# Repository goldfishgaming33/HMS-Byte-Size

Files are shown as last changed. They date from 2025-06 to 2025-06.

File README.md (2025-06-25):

# ABOUT

- I decided to take on this project when I realised I had nothing better to do over the summer
- I wanted to make use of skills I learnt while building a different device for a school competition which was a satellite in the size of a can
- I learnt to solder better, code better on the Raspberry Pi platform and design a PCB
- RC models and boats have always interested me, so I decided to combine the two to create HMS Byte Size
- The system will operate on the Raspberry Pi Zero 2W, communicating over 2.4GHz RF with a secondary Pi which will control the boat remotely
- I wasn't too confident with SMD and lacking a hot plate or any SMD capability, I decided to go with all through hole components

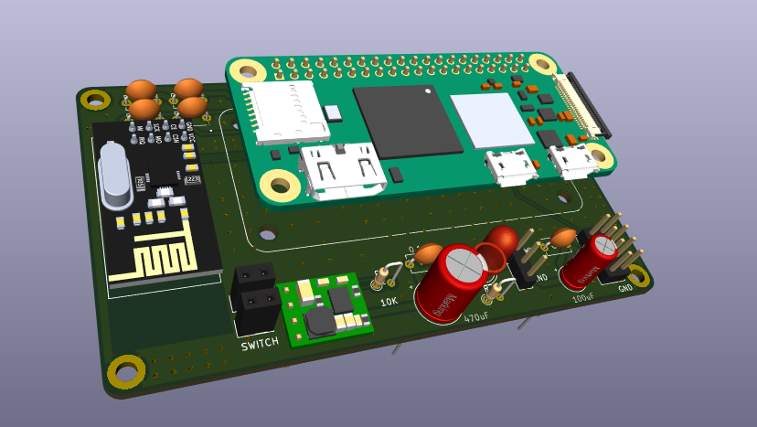
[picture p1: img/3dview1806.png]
3Dview

_LED will power to confirm the board is running_

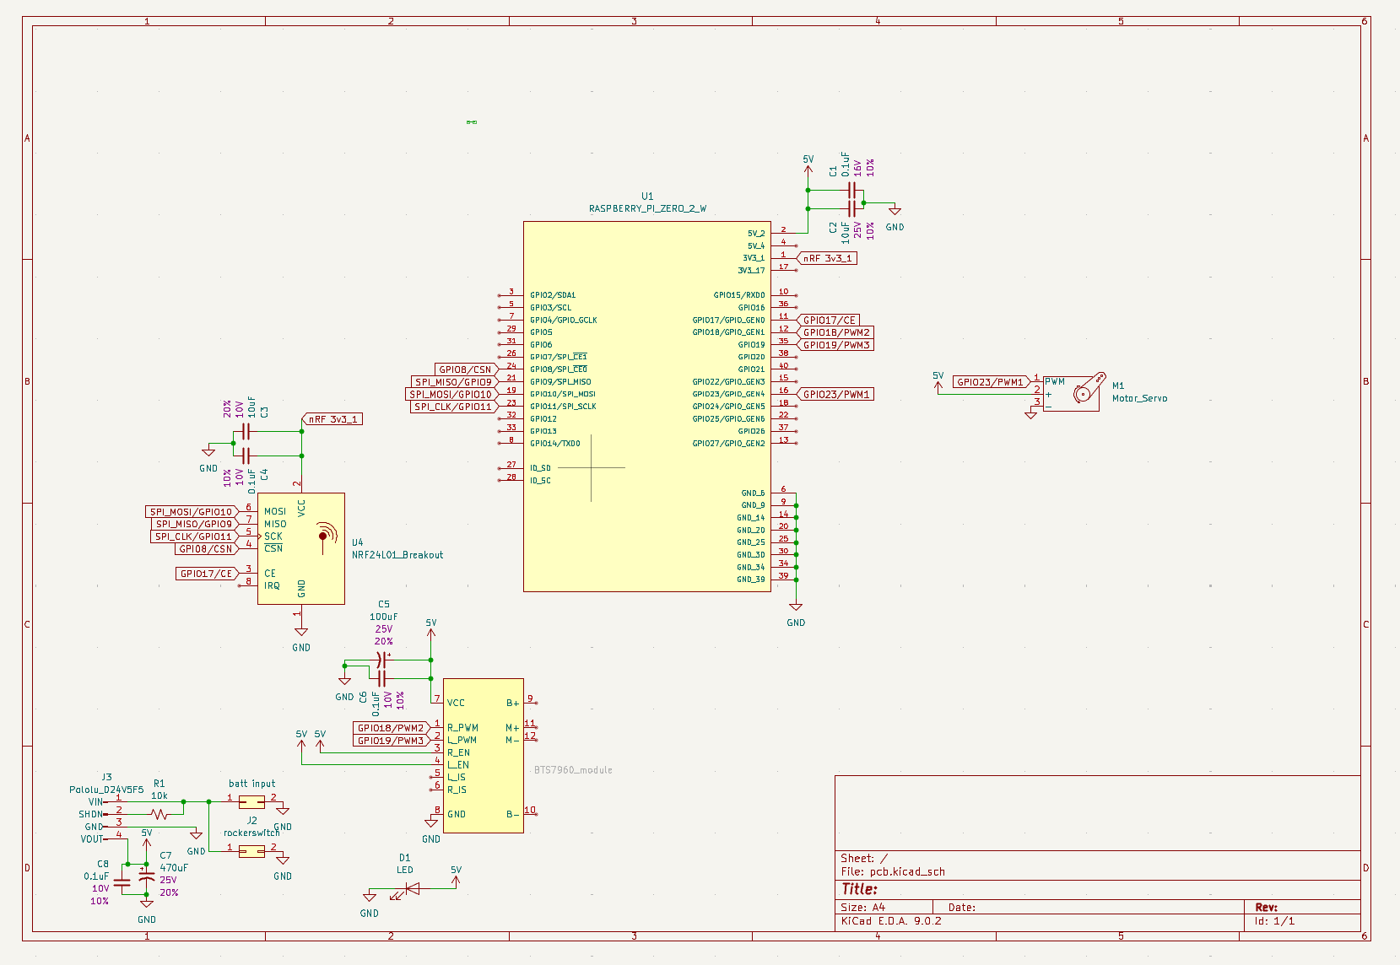
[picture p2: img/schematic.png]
schem

_Careful planning of how to power such project took place and resulted in numerous de-coupling capacitors, and others to manage current spikes and back-EMI_

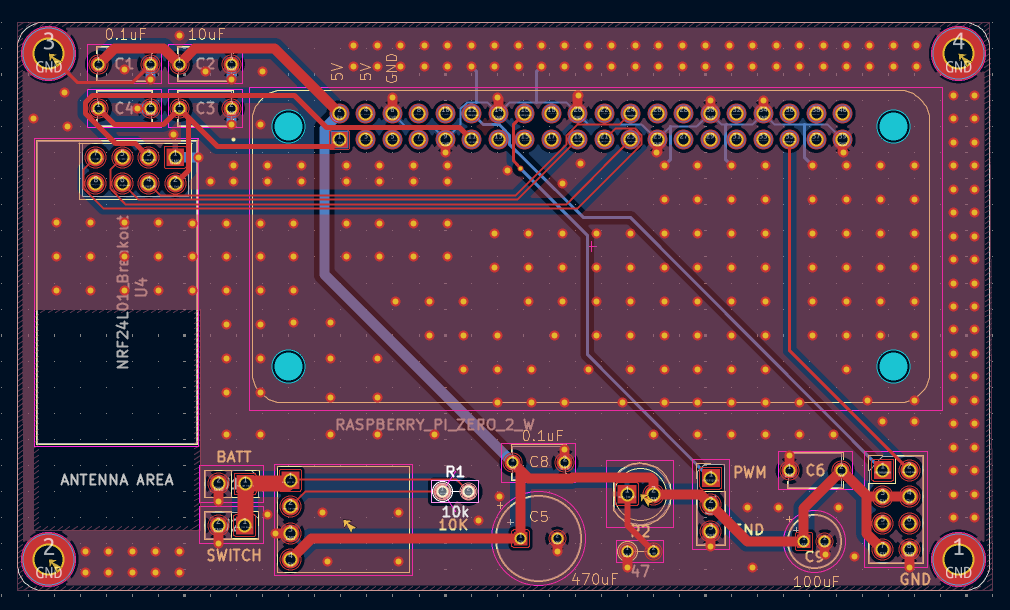
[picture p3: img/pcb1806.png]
pcb

_2-layer PCB composed of all through hole components, will full layer ground pours, and via stitching_

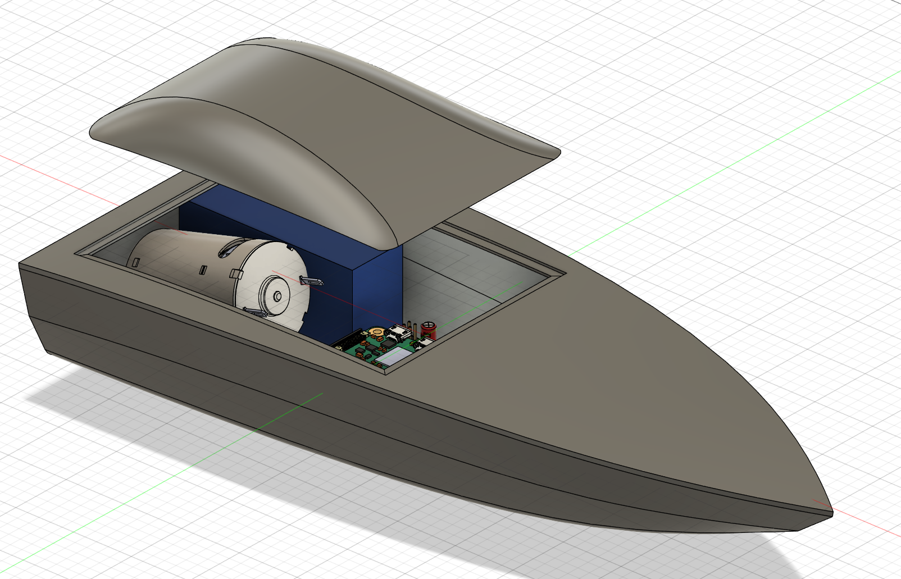
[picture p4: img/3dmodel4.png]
3dmodel

_Compact 3D printed design for easy assembly_

## Costs
It's looking rather costly

I've tried to stick to amazon and ali express for cheap components, but obviously I have doubts about reliability and whatnot.

Things like resistors and capacitors through MouserUK and RapidElectronics

## BOM

It's a bit messy, I just add as I go. All accurate though

https://1drv.ms/x/c/58d29176c16c150d/ESuSnoqv2EdMtOshy8H60zMBzeC2gvnFj-rfRvqEexovow?e=tm9gPX

Screenshot
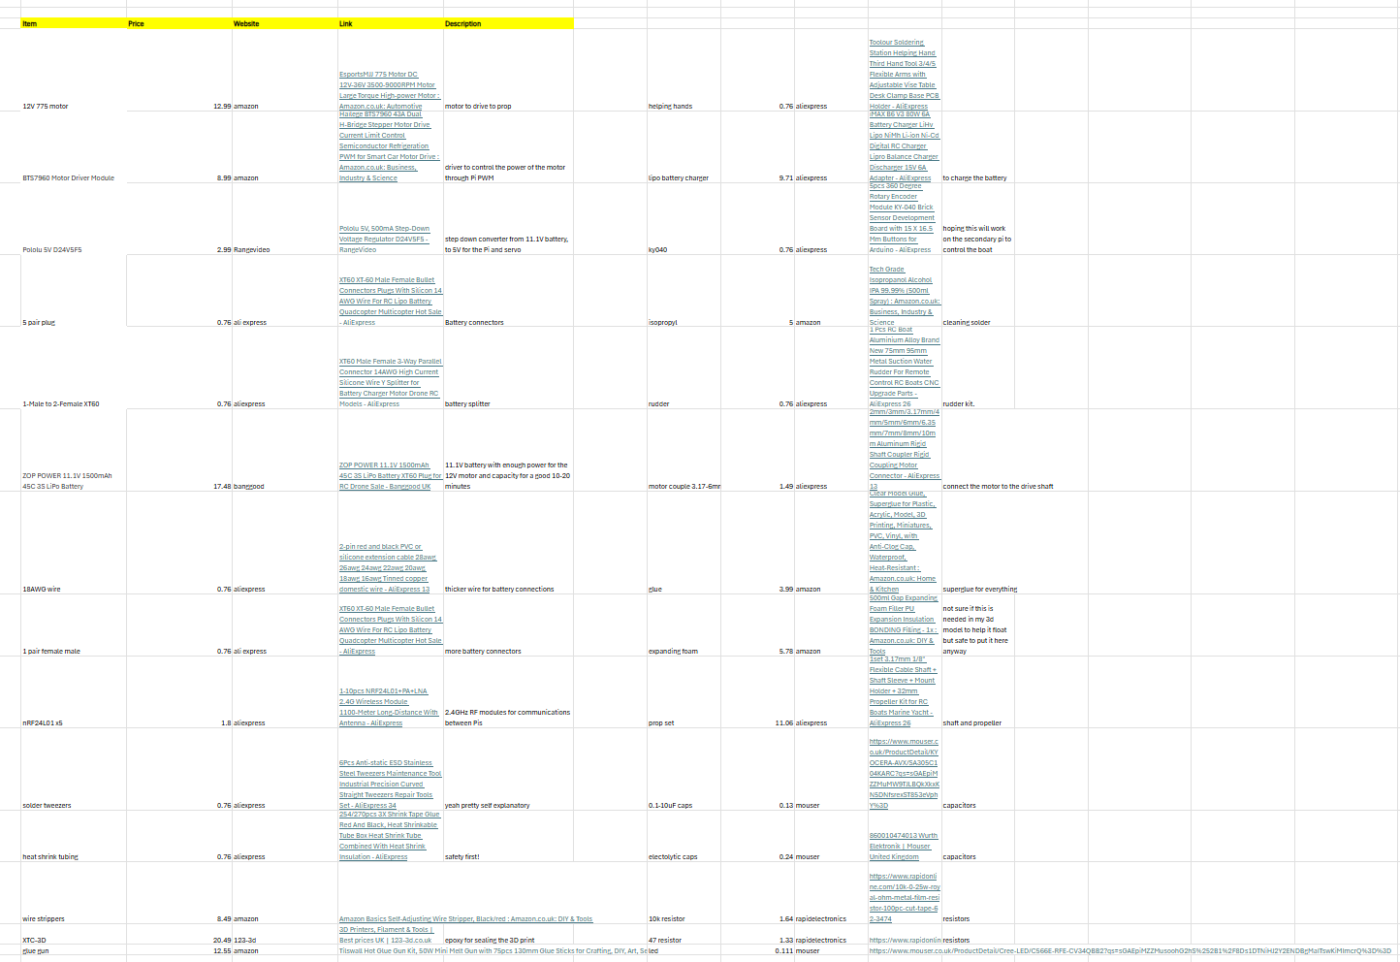
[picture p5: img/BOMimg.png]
BOM


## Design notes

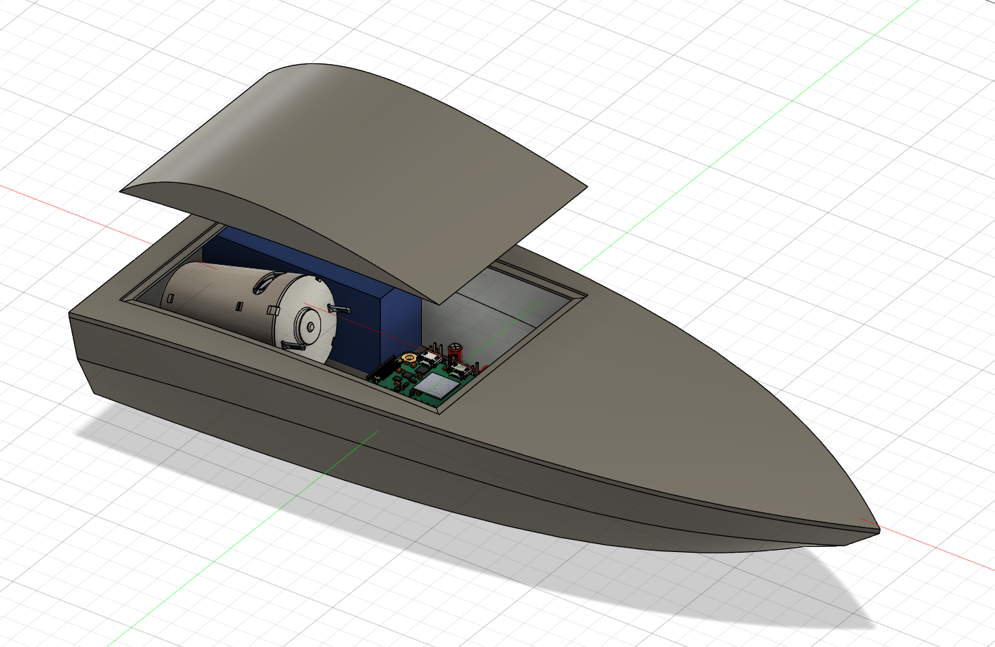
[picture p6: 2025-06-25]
img/3dmodel3.png

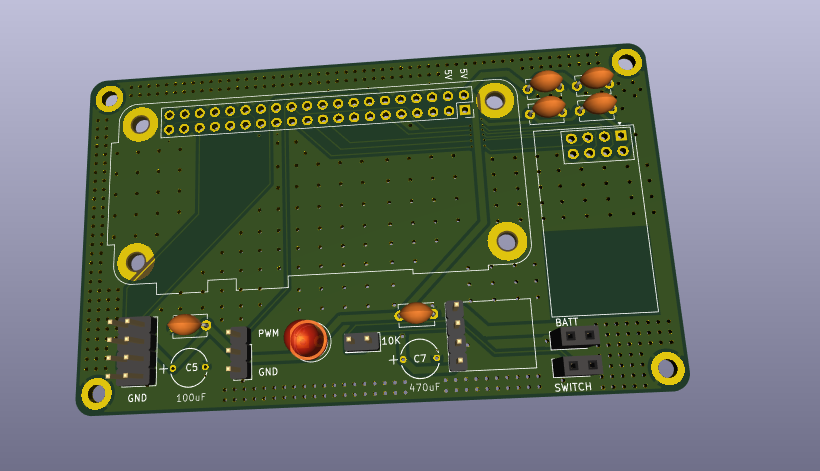
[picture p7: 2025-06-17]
img/3Dview.png

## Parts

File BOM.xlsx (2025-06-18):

Item | Price | Website | Link | Description
12V 775 motor | 12.99 | amazon | EsportsMJJ 775 Motor DC 12V-36V 3500-9000RPM Motor Large Torque High-power Motor : Amazon.co.uk: Automotive (https://www.amazon.co.uk/EsportsMJJ-12V-36V-3500-9000RPM-Torque-High-power/dp/B075D85KVV) | motor to drive to prop |  | helping hands | 0.76 | aliexpress | Toolour Soldering Station Helping Hand Third Hand Tool 3/4/5 Flexible Arms with Adjustable Vise Table Desk Clamp Base PCB Holder - AliExpress (https://www.aliexpress.com/item/1005007513733434.html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)
BTS7960 Motor Driver Module | 8.99 | amazon | Hailege BTS7960 43A Dual H-Bridge Stepper Motor Drive Current Limit Control Semiconductor Refrigeration PWM for Smart Car Motor Drive : Amazon.co.uk: Business, Industry & Science (https://www.amazon.co.uk/BTS7960-H-Bridge-Stepper-Semiconductor-Refrigeration/dp/B07Y4TTK3Z) | driver to control the power of the motor through Pi PWM |  | lipo battery charger | 9.71 | aliexpress | iMAX B6 V3 80W 6A Battery Charger LiHv Lipo NiMh Li-ion Ni-Cd Digital RC Charger Lipro Balance Charger Discharger 15V 6A Adapter - AliExpress (https://www.aliexpress.com/item/1005005231331856.html?businessType=ProductDetail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) | to charge the battery
Pololu 5V D24V5F5 | 2.99 | Rangevideo | Pololu 5V, 500mA Step-Down Voltage Regulator D24V5F5 - RangeVideo (https://www.rangevideo.com/products/pololu-5v-500ma-step-down-voltage-regulator-d24v5f5) | step down converter from 11.1V battery, to 5V for the Pi and servo |  | ky040 | 0.76 | aliexpress | 5pcs 360 Degree Rotary Encoder Module KY-040 Brick Sensor Development Board with 15 X 16.5 Mm Buttons for Arduino - AliExpress (https://www.aliexpress.com/item/1005005559054521.html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) | hoping this will work on the secondary pi to control the boat
5 pair plug | 0.76 | ali express | XT60 XT-60 Male Female Bullet Connectors Plugs With Silicon 14 AWG Wire For RC Lipo Battery Quadcopter Multicopter Hot Sale - AliExpress (https://www.aliexpress.com/item/1005003658392996.html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) | Battery connectors |  | isopropyl | 5 | amazon | Tech Grade Isopropanol Alcohol IPA 99.99% (500ml Spray) : Amazon.co.uk: Business, Industry & Science (https://www.amazon.co.uk/Grade-Isopropanol-Alcohol-99-99-500ml/dp/B08PD9P1VX) | cleaning solder
1-Male to 2-Female XT60 | 0.76 | aliexpress | XT60 Male Female 3-Way Parallel Connector 14AWG High Current Silicone Wire Y Splitter for Battery Charger Motor Drone RC Models - AliExpress (https://www.aliexpress.com/item/1005005725141150.html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) | battery splitter |  | rudder | 0.76 | aliexpress | 1 Pcs RC Boat Aluminium Alloy Brand New 75mm 95mm Metal Suction Water Rudder For Remote Control RC Boats CNC Upgrade Parts - AliExpress 26 (https://www.aliexpress.com/item/1005005873906106.html?businessType=ProductDetail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) | rudder kit.
ZOP POWER 11.1V 1500mAh 45C 3S LiPo Battery | 17.48 | banggood | ZOP POWER 11.1V 1500mAh 45C 3S LiPo Battery XT60 Plug for RC Drone Sale - Banggood UK (https://uk.banggood.com/ZOP-POWER-11_1V-1500mAh-45C-3S-LiPo-Battery-XT60-Plug-for-RC-Drone-p-1979030.html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) | 11.1V battery with enough power for the 12V motor and capacity for a good 10-20 minutes |  | motor couple 3.17-6mm | 1.49 | aliexpress | 2mm/3mm/3.17mm/4mm/5mm/6mm/6.35mm/7mm/8mm/10mm Aluminum Rigid Shaft Coupler Rigid Coupling Motor Connector - AliExpress 13 (https://www.aliexpress.com/item/4000196552485.html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) | connect the motor to the drive shaft
18AWG wire | 0.76 | aliexpress | 2-pin red and black PVC or silicone extension cable 28awg 26awg 24awg 22awg 20awg 18awg 16awg Tinned copper domestic wire - AliExpress 13 (https://www.aliexpress.com/item/1005007251965003.html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) | thicker wire for battery connections |  | glue | 3.99 | amazon | Plastic Glue 30 g, Clear Model Glue, Superglue for Plastic, Acrylic, Model, 3D Printing, Miniatures, PVC, Vinyl, with Anti-Clog Cap, Waterproof, Heat-Resistant : Amazon.co.uk: Home & Kitchen (https://www.amazon.co.uk/Superglue-Miniatures-Anti-Clog-Waterproof-Heat-Resistant/dp/B0DRJNFVZ9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) | superglue for everything
1 pair female male | 0.76 | ali express | XT60 XT-60 Male Female Bullet Connectors Plugs With Silicon 14 AWG Wire For RC Lipo Battery Quadcopter Multicopter Hot Sale - AliExpress (https://www.aliexpress.com/item/1005003658392996.html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) | more battery connectors |  | expanding foam | 5.78 | amazon | 500ml Gap Expanding Foam Filler PU Expansion Insulation BONDING Filling - 1x : Amazon.co.uk: DIY & Tools (https://www.amazon.co.uk/Expanding-Expansion-Insulation-BONDING-Filling/dp/B093DZT8TZ) | not sure if this is needed in my 3d model to help it float but safe to put it here anyway
nRF24L01 x5 | 1.8 | aliexpress | 1-10pcs NRF24L01+PA+LNA 2.4G Wireless Module 1100-Meter Long-Distance With Antenna - AliExpress (https://www.aliexpress.com/item/1005007796985331.html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) | 2.4GHz RF modules for communications between Pis |  | prop set | 11.06 | aliexpress | 1set 3.17mm 1/8" Flexible Cable Shaft + Shaft Sleeve + Mount Holder + 32mm Propeller Kit for RC Boats Marine Yacht - AliExpress 26 (https://www.aliexpress.com/item/1005001349058436.html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) | shaft and propeller
solder tweezers | 0.76 | aliexpress | 6Pcs Anti-static ESD Stainless Steel Tweezers Maintenance Tool Industrial Precision Curved Straight Tweezers Repair Tools Set - AliExpress 34 (https://www.aliexpress.com/item/1005007425589207.html?mp=1) | yeah pretty self explanatory |  | 0.1-10uF caps | 0.13 | mouser | https://www.mouser.co.uk/ProductDetail/KYOCERA-AVX/SA305C104KARC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 | capacitors
heat shrink tubing | 0.76 | aliexpress | 254/270pcs 3X Shrink Tape Glue Red And Black, Heat Shrinkable Tube Box Heat Shrink Tube Combined With Heat Shrink Insulation - AliExpress (https://www.aliexpress.com/item/1005006511088545.html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) | safety first! |  | electolytic caps | 0.24 | mouser | 860010474013 Wurth Elektronik | Mouser United Kingdom (https://www.mouser.co.uk/ProductDetail/Wurth-Elektronik/860010474013?qs=0KOYDY2FL2%2Ftqmj8vEDl2w%3D%3D) | capacitors
wire strippers | 8.49 | amazon | Amazon Basics Self-Adjusting Wire Stripper, Black/red : Amazon.co.uk: DIY & Tools (https://www.amazon.co.uk/AmazonBasics-DS-SWP-Self-Adjusting-Wire-Stripper/dp/B07TS6KCXD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) |  |  | 10k resistor | 1.64 | rapidelectronics | https://www.rapidonline.com/10k-0-25w-royal-ohm-metal-film-resistor-100pc-cut-tape-62-3474 | resistors
XTC-3D | 20.49 | 123-3d | 3D Printers, Filament & Tools | Best prices UK | 123-3d.co.uk (https://www.123-3d.co.uk/SmoothOn-Smooth-On-XTC-3D-coating-181-gr-A-B-i8654.html) | epoxy for sealing the 3D print |  | 47 resistor | 1.33 | rapidelectronics | https://www.rapidonline.com/47r-0-25w-royal-ohm-metal-film-resistor-100pc-cut-tape-62-3418 | resistors
glue gun | 12.55 | amazon | Tilswall Hot Glue Gun Kit, 50W Mini Melt Gun with 75pcs 130mm Glue Sticks for Crafting, DIY, Art, Sealing, Home Repairs, Cards, and Glass : Amazon.co.uk: DIY & Tools (https://www.amazon.co.uk/Tilswall-Quickly-Patents-Sealing-Repairs/dp/B07TD35L5R?sp_csd=d2lkZ2V0TmFtZT1zcF9hdGY) |  |  | led | 0.111 | mouser | https://www.mouser.co.uk/ProductDetail/Cree-LED/C566E-RFE-CV34QBB2
 |  |  |  |  | Mfr Part Number | Manufacturer Part Number | Mouser Part Number | Manufacturer Name | Description | Quantity 1 | Unit Price 1

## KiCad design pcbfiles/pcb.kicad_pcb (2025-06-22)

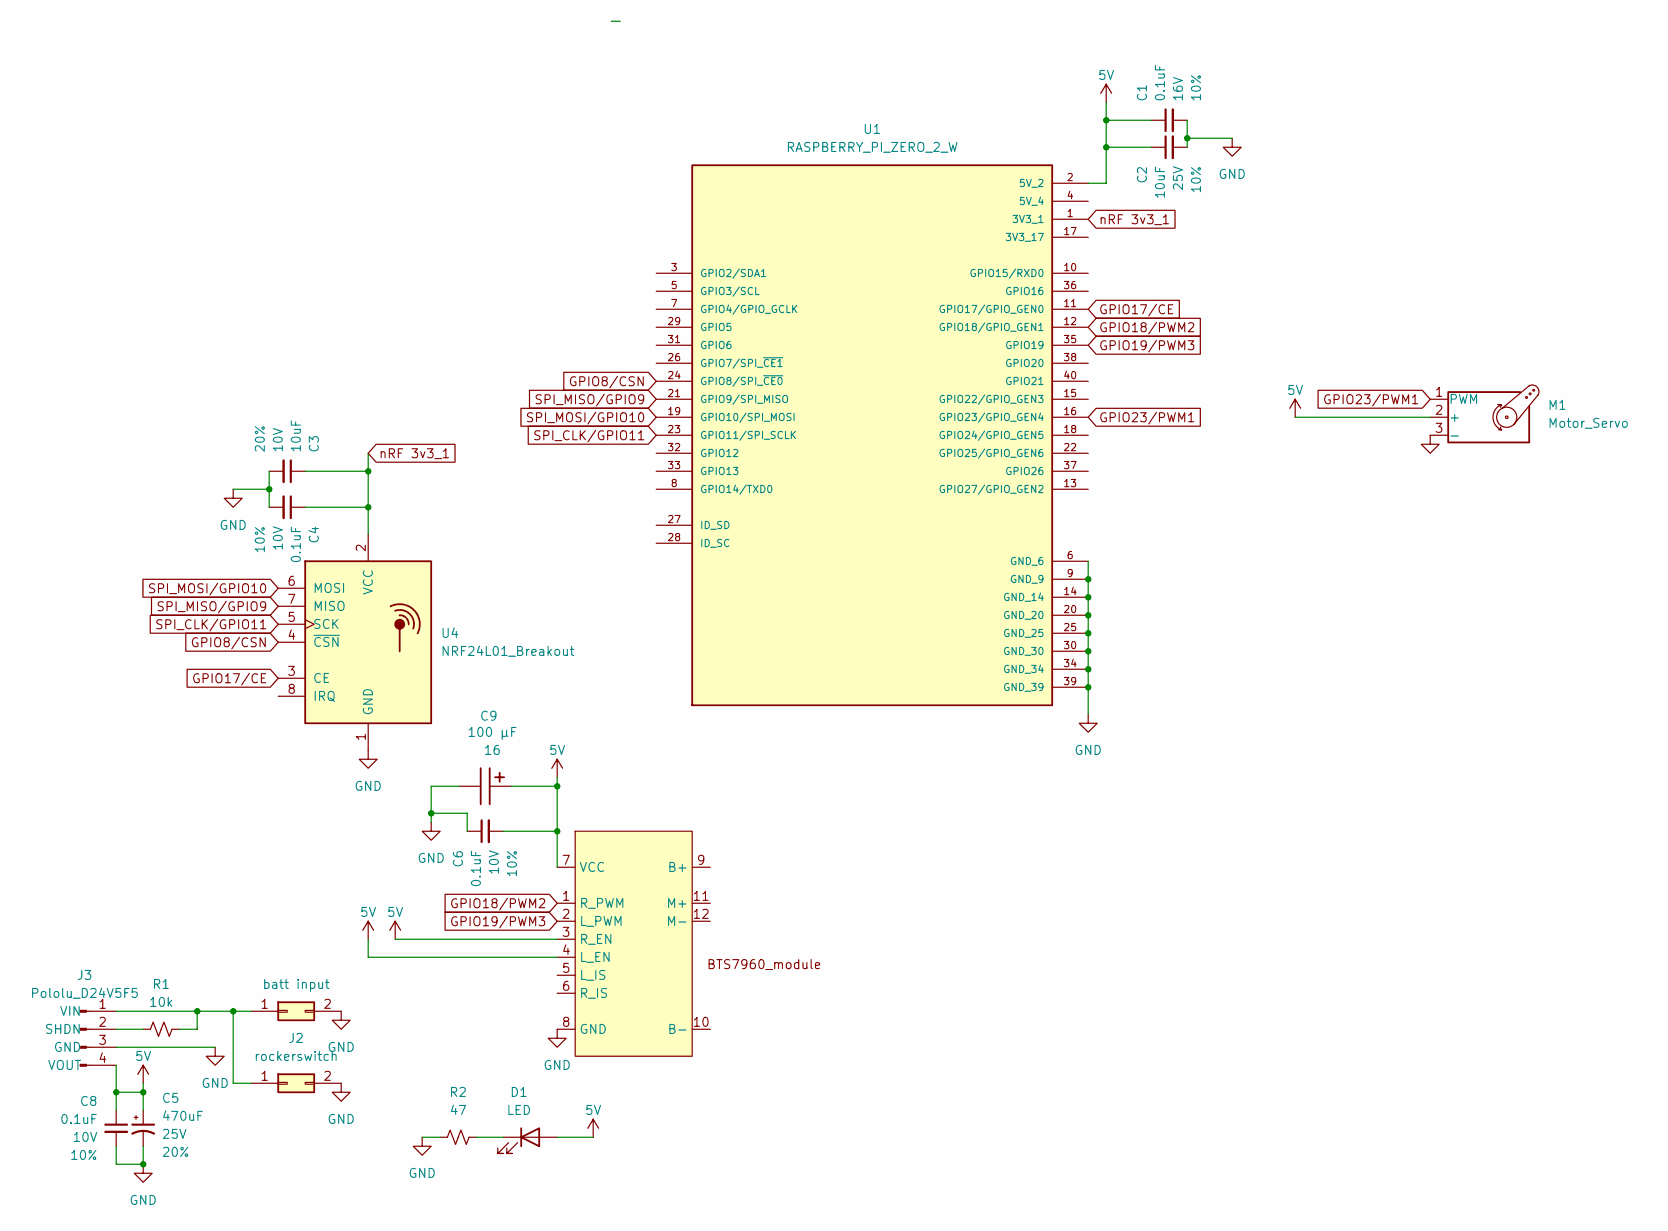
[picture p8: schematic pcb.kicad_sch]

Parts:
C1: 0.1uF; C_Disc_D5.1mm_W3.2mm_P5.00mm; Voltage 16V; Tolerance 10%
C2: 10uF; C_Disc_D5.1mm_W3.2mm_P5.00mm; Voltage 25V; Tolerance 10%
C3: 10uF; C_Disc_D5.1mm_W3.2mm_P5.00mm; Voltage 10V; Tolerance 20%
C4, C6, C8: 0.1uF; C_Disc_D5.1mm_W3.2mm_P5.00mm; Voltage 10V; Tolerance 10%
C5: 470uF; CP_Wurth_WCAP-ATG8-P3.5D8L11.5; Voltage 25V; Tolerance 20%
C9: P2D5L11_860010372006; CP_Wurth_WCAP-ATG8-P2D5L11; Voltage 16; Part Number 860010372006
D1: LED; LED_D5.0mm
J1: batt input; PinSocket_2x01_P2.54mm_Vertical
J2: rockerswitch; PinSocket_2x01_P2.54mm_Vertical
J3: Pololu_D24V5F5; Converter_DCDC_Pololu_D24V5Fx_Horizontal (1)
M1: Motor_Servo; PinHeader_1x03_P2.54mm_Vertical
R1: 10k; R_Axial_DIN0204_L3.6mm_D1.6mm_P2.54mm_Vertical
R2: 47; R_Axial_DIN0204_L3.6mm_D1.6mm_P2.54mm_Vertical; Tolerance 1%
U1: RASPBERRY_PI_ZERO_2_W; MODULE_RASPBERRY_PI_ZERO_2_W; PARTREV April 2024
U2: PinHeader_2x04_P2.54mm_Vertical
U4: NRF24L01_Breakout; nRF24L01_Breakout

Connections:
5V: C1.1, C2.1, C5.1, C6.2, C8.1, C9.1, D1.2 (A), J3.4 (VOUT), M1.2 (+), U1.2 (5V_2), U2.3 (R_EN), U2.4 (L_EN), U2.7 (VCC)
GND: C1.2, C2.2, C3.2, C4.2, C5.2, C6.1, C8.2, C9.2, J1.2, J2.2, J3.3 (GND), M1.3 (-), R2.1, U1.6 (GND_6), U1.9 (GND_9), U1.14 (GND_14), U1.20 (GND_20), U1.25 (GND_25), U1.30 (GND_30), U1.34 (GND_34), U1.39 (GND_39), U2.8 (GND), U4.1 (GND)
GPIO8/CSN: U1.24 (GPIO8/SPI_~CE0), U4.4 (~CSN)
GPIO17/CE: U1.11 (GPIO17/GPIO_GEN0), U4.3 (CE)
GPIO18/PWM2: U1.12 (GPIO18/GPIO_GEN1), U2.1 (R_PWM)
GPIO19/PWM3: U1.35 (GPIO19), U2.2 (L_PWM)
GPIO23/PWM1: M1.1 (PWM), U1.16 (GPIO23/GPIO_GEN4)
unnamed: D1.1 (K), R2.2
unnamed: J1.1, J2.1, J3.1 (VIN), R1.2
unnamed: J3.2 (SHDN), R1.1
SPI_CLK/GPIO11: U1.23 (GPIO11/SPI_SCLK), U4.5 (SCK)
SPI_MISO/GPIO9: U1.21 (GPIO9/SPI_MISO), U4.7 (MISO)
SPI_MOSI/GPIO10: U1.19 (GPIO10/SPI_MOSI), U4.6 (MOSI)
nRF 3v3_1: C3.1, C4.1, U1.1 (3V3_1), U4.2 (VCC)

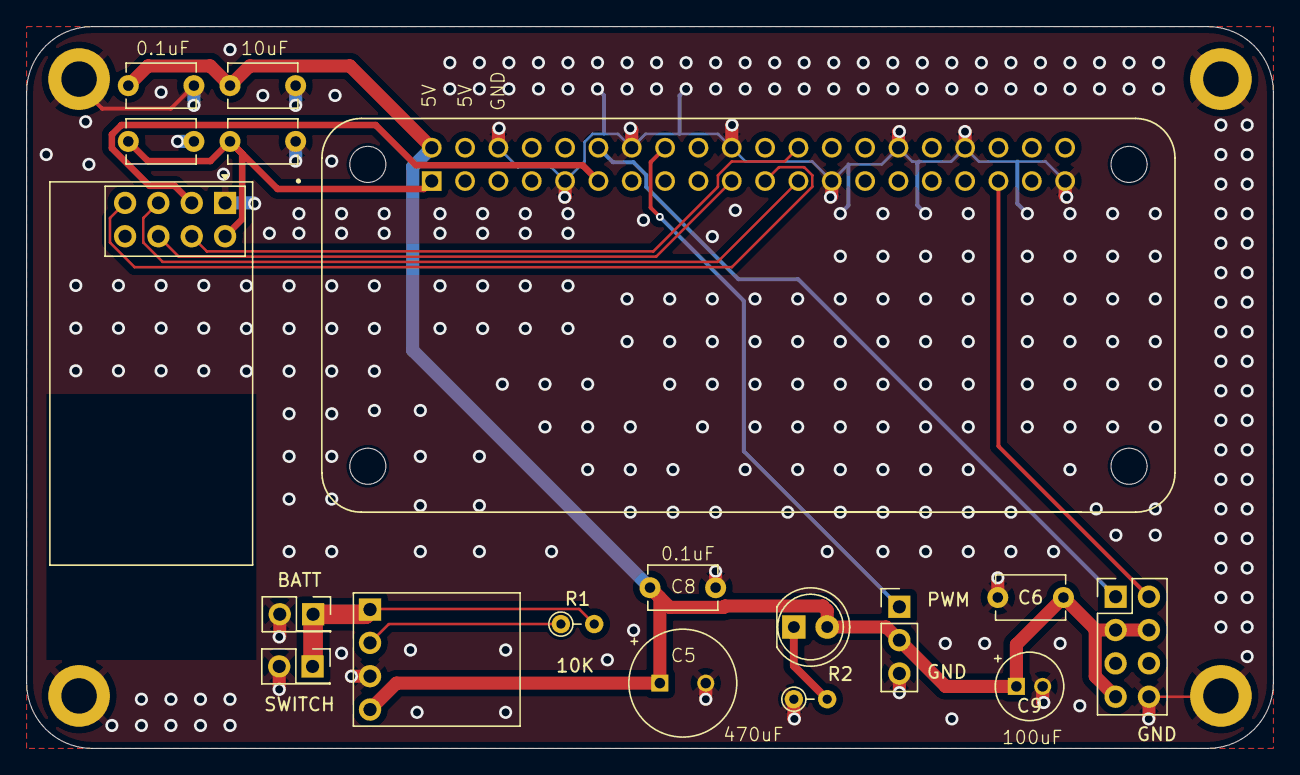
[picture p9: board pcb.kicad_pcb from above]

Board: 2 copper layers, 95.0 x 55.0 mm, 18 parts (0 on the bottom side), 14 nets.

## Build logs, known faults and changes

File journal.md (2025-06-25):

---
title: HMS Byte Size
author: "Alexander Golder"
description: "A RC boat inspired by a school competition, built on the Raspberry Pi platform"
created_at: 2025-06-07
---
- Time spent is cumulative 

## Saturday 7th June
Parts list finalised and BOM updated.

Total cost far exceeds what I was hoping. Let's hope it works

Time spent: 2 hours

## Tuesday 17th June
Finalising my PCB design to accommodate the Pi Zero 2W, nRF module and other parts

I've had to learn about capacitors and where to use them to improve the longevity and reliability of my RC boat. 

Experimented with ground planes and I think I've figured that out to avoid ground loops
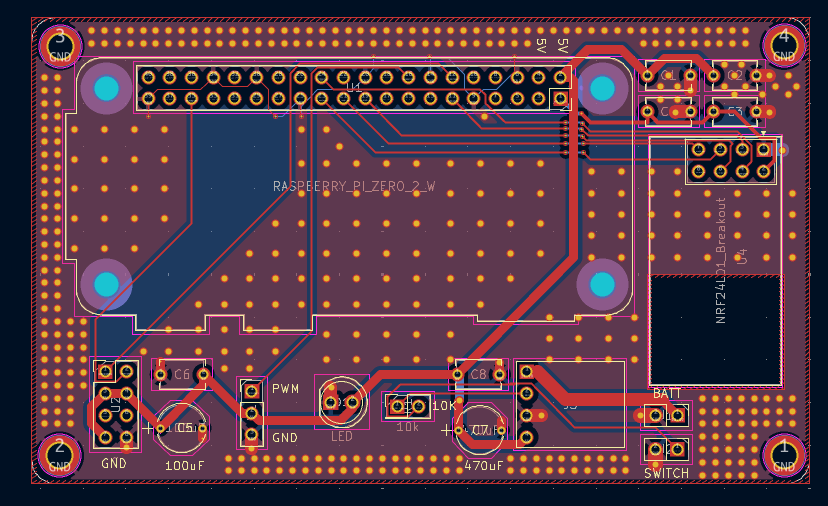
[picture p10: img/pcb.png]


_Almost finished PCB_

Now I need to begin CAD to build accommodation for all the components.

Time spend: 5 hours

## Wednesday 18th June
Added a readme and BOM together in one file. I reviewed a couple of other projects on the highway to see why people are being rejected, and hopefully I'm going to avoid that!

Asked a friend for some advice and made amends to my PCB, namely adding a resistor for me LED, and populating 3D models. Also, I had to basically re-do the PCB design because one of the footprints I was using was wrong...
PCB View
_Pretty sure it's finished now_
3dview
_Populated 3D model_

Time spent: 8 hours

## Saturday 21st and Sunday 22nd June
Basically taught myself CAD. Designs on the way.

## Monday 23rd June
My CAD model is beginning to take shape.
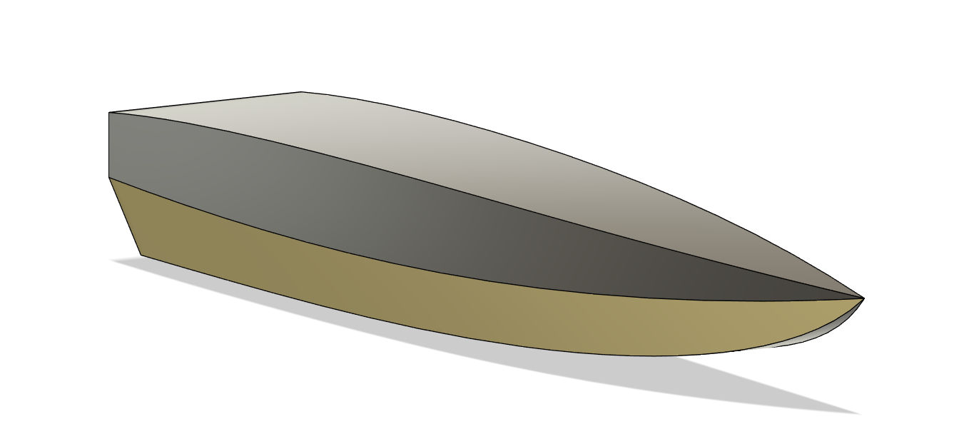
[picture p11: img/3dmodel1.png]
3dmodel


Time spent 9.5 hours

## Tuesday 24th June
developed the CAD model further. I need to figure out how to add mounts inside the hull for the components, and how to create a lid to seal it all in.
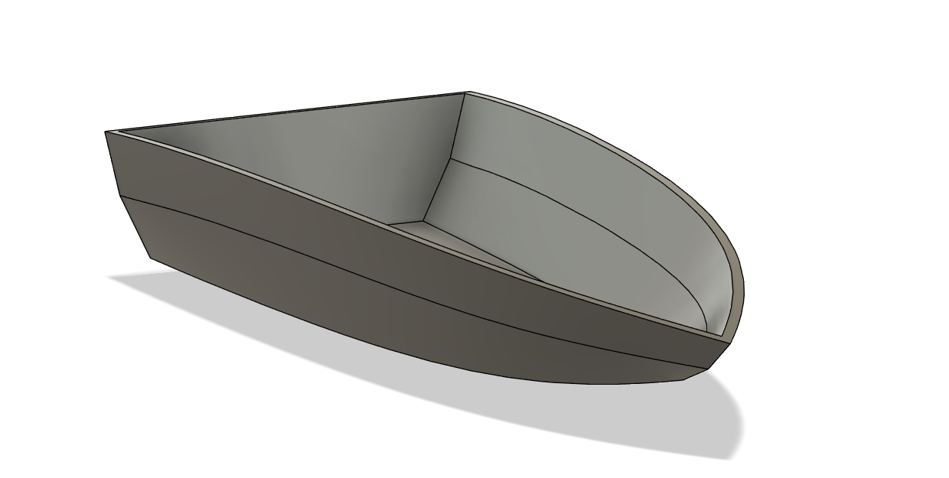
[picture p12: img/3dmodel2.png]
3dmodel


Time spent 10.5 hours

## Wednesday 25th June
Finished up the CAD model with the parts. Ready for submission!
3dmodel

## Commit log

2025-06-07 Add files via upload
    BOM and PCB files added
    [BOM.xlsx, pcb-DESKTOP-80JQAES.kicad_sch, pcb.kicad_pcb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]
2025-06-17 Add files via upload
    added updated pcb files
    [pcb.kicad_pcb, pcb.kicad_sch]
2025-06-18 updated journal and README.md, added new images and BOM
    [BOM.xlsx]
2025-06-22 Add files via upload
    added the update pcb files in one folder
    [pcb.kicad_pcb, pcb.kicad_sch]
2025-06-25 updated journal and README.md, added new images and added CAD files
